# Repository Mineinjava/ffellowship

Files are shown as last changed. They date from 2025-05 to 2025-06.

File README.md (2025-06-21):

# ffellowship
Frequency Fellowship: Examining Radio Wave Propagation from a High Altitude Balloon
---

This is a project for Hack Club's [Apex](https://apex.hackclub.com),
made by:
- [Marcus Kauffman](https://kauffman.tools) KN6UYL (@mineinjava)
- Hudson Hilal (@hhilal123)
- Joshua Truman (@jstruman4929)

We initially had two project ideas for Apex: this and dropping what was
effectively a lawn dart from 100,000 feet. After the lawn dart project
was rejected, we submitted this project.

Many high altitude balloons (HABs) have been launched, almost all of
which have some sort of tracker that transmits the balloon's location.
These transmissions are received by stations on the ground and then
uploaded to the internet, from which we can view the locations of
receiving stations for analysis. Our goal for this project is to study
the differences between different tracker design techniques,
specifically:

- Does radio band selection influence likelihood of reception?
    - Receiving stations on the 2m band are much more common than those
      on the 20m band, but 20m transmissions theoretically travel
      farther.
- There are three common methods of modulating signals:
    - Connecting to a dedicated radio for transmission
    - Using a MS5351M or similar clock generator IC
    - Using [fancy PLL](https://github.com/kaduhi/pico-fractional-pll)
      to "bit-bang" the radio waveform

    **Question: do these three modulation methods have a significant
    difference in quality and therefore propagation?**
- How do different antenna designs affect propagation.

Due to customs issues, we were only able to test the PLL tracker 
with three antenna wavelengths. Two of the frequencies had issues 
(unresolved ATM), so we instead analyzed the effect of height on 
radio wave propagation.

As suggested above, this project can easily be divided into three
"sub-projects":

## 1. Use of the MS5351M Clock Generator IC.

This subproject revolves around the MS5351M clock generator. It features
a custom PCB. Note that this tracker will transmit on both the 20m and
2m bands because the MS5351M has multiple clock generators.

This tracker has quite a few features, many of which are to support
ultra-low power operation, as is common with this style of tracker:

- GPS
- Temperature/pressure sensor
- Shunt
- 3v3 buck-boost converter
- power supervisor to restart the pico
- Sensors can be powered off to conserve power.

This PCB is designed around the Raspberry Pi Pico due to its rigorous
testing and ease of integration. It also features mainly 1206 components
to aid in manual reflow soldering of the PCB.

See the dPicoTracker/ directory for more info.





## 2. Use of PLL:

This subproject uses the Raspberry Pi Pico to generate RF signals,
*without the use of a dedicated radio/chip*. It is by far the simplest
design and features a power supervisor, optional low-pass filter, 
battery measurement circuitry, as well as a GPS which is essential 
for correcting oscillator drift.





## 3. Use of a Dedicated HT Radio.

This subproject uses a Raspberry Pi Zero W and a custom PCB to connect
to a HT, which will be stripped down to save weight. 

The PCB consists of a voltage regulator to power the Pi and a 555 timer
circuit to ensure that transmissions are limited in time (in case
of a software crash).





## Integration:

*coming soon*

## Project Status:

*coming soon*

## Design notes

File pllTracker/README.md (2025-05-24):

# Tracker using PLL

This tracker uses fractional PLL to generate RF on the 20m band.

## BOM:

| Id  | Designator | Footprint | Quantity | Designation | Supplier and ref |
|-----|---|---|---|---|---|
| 1 | C15 | C_1206_3216Metric | 1 | 300pF | C5449026 |
| 2 | C14,C16 | C_1206_3216Metric | 2 | 180pF | C3832761 |
| 3 | R6 | C_1206_3216Metric | 1 | 100kΩ | C137393 |
| 4 | U7 | SOT-23_ONS | 1 | MAX809STRG | C9965 |
| 6 | R1 | C_1206_3216Metric | 1 | 10kΩ | C132649 |
| 7 | L5,L4 | L_1206_3216Metric | 2 | 560nH | C13585 |
| 10  | IC1 | ATGM336H5N31 | 1 | ATGM336H-5N31 | C2940946 |
| 11  | C8 | C_1206_3216Metric | 2 | 100nF | C137393 |
| 13  | Q1, Q2 | Q_SOT-23 | 1 | AO3401A | C15127 |
| 13  | C7 | C_1206_3216Metric | 1 | 1nF | C23631 |
| 14  | R5 | D_1206_3216Metric | 1 | 200kΩ | C114937 |

Additionally:
- 1 GPS antenna
- 1 20m antenna
- 1 Raspberry Pi Pico

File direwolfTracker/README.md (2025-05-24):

# Direwolf-powered Tracker

This tracker uses direwolf to communicate with an external radio like a
HT.

## BOM:

| Id  | Designator | Footprint | Quantity | Designation | Supplier and ref |
|-----|---|---|---|---|---|
| 1 | C2, C1, C3 | C_1206_3216Metric | 3 | 10µF | C13585 |
| 3 | Q1 | Q_SOT-23 | 1 | MMBT2222A | C82460 |
| 4 | C20, C19, C21 | C_1206_3216Metric | 3 | 100nF | C82460 |
| 7 | U1 | Texas_R-PDSO-G6 | 1 | TPS61222DCK | C116461 |
| 9 | R1 | R_1206_3216Metric | 1 | 10kΩ | C132649 |
| 10  | R3 | R_1206_3216Metric | 1 | 2.7kΩ | C2930416 |
| 12  | IC1 | ATGM336H5N31 | 1 | ATGM336H-5N31 | C2940946 |
| 13  | R2 | R_1206_3216Metric | 1 | 100kΩ | C2930416 |
| 14  | U2 | DIP-8_W7.62mm | 1 | ICM7555xP | C22461592 |
| 15  | R4 | R_1206_3216Metric | 1 | 1MΩ | C108083 |
| 16  | L1 | L_1206_3216Metric | 1 | 4.7µH | C13585 |

Additionally:
- 1 Raspberry Pi Zero
- 1 GPS Antenna
- 1 micro usb sound card
- 1 TRRS 3.5mm cable
- 1 TRS 3.5mm cable
- 1 TRS 2.5mm cable
- 1 external radio

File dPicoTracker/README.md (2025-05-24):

# Tracker With MS5351M IC

This tracker uses the MS5351M IC to generate RF.

## BOM:

| Id  | Designator | Footprint | Quantity | Designation | Supplier and ref | 
|-----|---|---|---|---|---|
| 1 | L1 | L_1206_3216Metric | 1 | 4.7µH | C13585 |
| 2 | C14, C16 | C_1206_3216Metric | 2 | 18pF | C565686 |
| 3 | L4, L5 | L_1206_3216Metric | 2 | 56nH | C13585 |
| 4 | U7 | SOT-23_ONS | 1 | MAX809STRG | C9965 |
| 6 | U8 | Bosch_LGA-8_2x2.5mm_P0.65mm | 1 | BMP280 | C83291 |
| 7 | Y1 | MSOP-10_3x3mm_P0.5mm | 1 | Si5351A-B-GT | C1509083 |
| 8 | C9, C19, C1, C8, C17, C18, C10 | C_1206_3216Metric | 7 | 100nF | C24497 |
| 10  | Y2 | Crystal_SMD_2520-4Pin_2.5x2.0mm | 1 | C132296 | C132296 |
| 11  | L3, L2 | L_1206_3216Metric | 2 | 560nH | C13585 |
| 12  | R6 | C_1206_3216Metric | 1 | 100kΩ | C137393 |
| 13  | Q1, Q2 | Q_SOT-23 | 2 | AO3401A | C15127 |
| 15  | R8, R14, R15, R11, R9, R12 | R_1206_3216Metric | 6 | 10kΩ | C132649 |
| 16  | C15 | C_1206_3216Metric | 1 | 30pF | C1905 |
| 17  | C12 | C_1206_3216Metric | 1 | 300pF | C5449026 |
| 18  | C5 | C_1206_3216Metric | 1 | 10µF | C13585 |
| 19  | C11, C13 | C_1206_3216Metric | 2 | 180pF | C3832761 |
| 20  | IC1 | ATGM336H5N31 | 1 | ATGM336H-5N31 | C2940946 |
| 21  | U3, U4 | SOT-23-3_L2.9-W1.6-P1.90-LS2.8-BR | 2 | CJ431 | C3113 |
| 22  | R7 | C_1206_3216Metric | 1 | 10kΩ | C132649 |
| 23  | U5 | Texas_R-PDSO-G6 | 1 | TPS61221DCK | C2865756 |
| 24  | C7 | C_1206_3216Metric | 1 | 1nF | C23631 |
| 25  | R5 | D_1206_3216Metric | 1 | 200kΩ | C114937 |

Additionally:
- 1x GPS antenna
- 1x 2m antenna
- 1x 20m antenna
- 1x Raspberry Pi Pico

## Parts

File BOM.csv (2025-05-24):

Comment | Designator | Footprint | LCSC Part # | Quantity
4.7µH | L1 | L_1206_3216Metric | C13585 | 2
18pF | C14 C16 | C_1206_3216Metric | C565686 | 2
56nH | L4 L5 | L_1206_3216Metric | C13585 | 2
MAX809STRG | U7 | U_SOT-23_ONS | C9965 | 2
BMP280 | U8 | Bosch_LGA-8_2x2.5mm_P0.65mm | C83291 | 1
Si5351A-B-GT | Y1 | MSOP-10_3x3mm_P0.5mm | C1509083 | 1
100nF | C9 C19 C1 C8 C17 C18 C10 C20 C21 | C_1206_3216Metric | C24497 | 10
C132296 | Y2 | Crystal_SMD_2520-4Pin_2.5x2.0mm | C132296 | 1
560nH | L2 L3 L4 L5 | L_1206_3216Metric | C13585 | 4
100kΩ | R6 R2 | C_1206_3216Metric | C137393 | 2
AO3401A | Q1 Q2 Q1 | Q_SOT-23 | C15127 | 3
10kΩ | R1 R7 R8 R9 R11 R12 R14 | R_1206_3216Metric | C132649 | 8
30pF | C15 | C_1206_3216Metric | C1905 | 1
300pF | C12 C15 | C_1206_3216Metric | C5449026 | 2
10µF | C2 C1 C3 C5 | C_1206_3216Metric | C13585 | 4
180pF | C11 C13 C14 C16 | C_1206_3216Metric | C3832761 | 4
ATGM336H-5N31 | IC1 IC1 IC1 | ATGM336H5N31 | C2940946 | 3
CJ431 | U3 U4 | SOT-23-3_L2.9-W1.6-P1.90-LS2.8-BR | C3113 | 2
TPS61221DCK | U5 | Texas_R-PDSO-G6 | C2865756 | 1
1nF | C7 C7 | C_1206_3216Metric | C23631 | 2
200kΩ | R5 R5 | D_1206_3216Metric | C114937 | 2
MMBT2222A | Q1 | Q_SOT-23 | C82460 | 1
TPS61222DCK | U1 | Texas_R-PDSO-G6 | C116461 | 1
2.7kΩ | R3 | R_1206_3216Metric | C2930416 | 1
ICM7555xP | U2 | DIP-8_W7.62mm | C22461592 | 1
1MΩ | R4 | R_1206_3216Metric | C108083 | 1

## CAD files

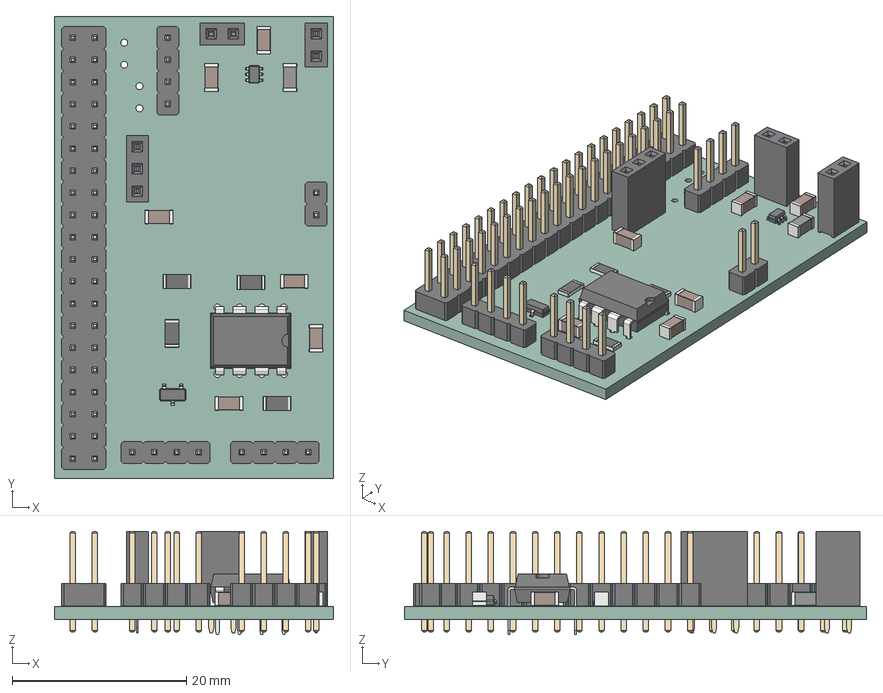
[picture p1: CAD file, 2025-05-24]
direwolfTracker/direwolfTracker.step
32.0 x 53.0 x 11.8 mm
C_1206_3216Metric x 6
PinSocket_1x02_P2.54mm_Vertical x 2
Q_SOT-23
PinHeader_1x04_P2.54mm_Vertical x 3
PinSocket_1x03_P2.54mm_Vertical
SOT-363_SC-70-6
R_1206_3216Metric x 4
PinHeader_1x02_P2.54mm_Vertical
DIP-8_W7.62mm
L_1206_3216Metric
PinHeader_2x20_P2.54mm_Vertical
direwolfTracker_PCB

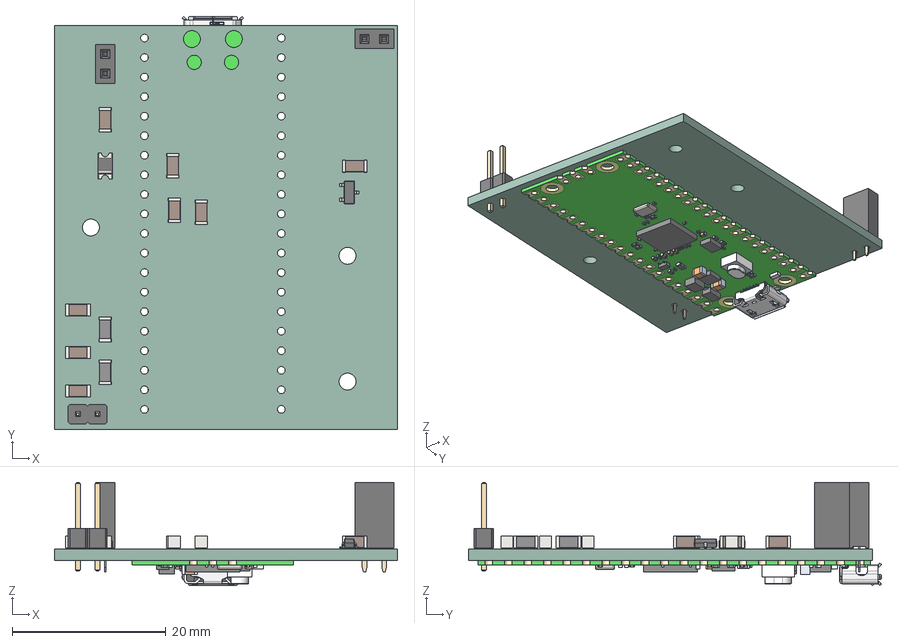
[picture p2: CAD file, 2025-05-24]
pllTracker/pllTracker.step
44.6 x 53.7 x 13.4 mm
C_1206_3216Metric x 8
Q_SOT-23
PinSocket_1x02_P2.54mm_Vertical x 2
L_1206_3216Metric x 2
PinHeader_1x02_P2.54mm_Vertical
D_1206_3216Metric
PCB, Raspberry Pi Pico-R3
MicroUSB Port, Raspberry Pi Pico-R3
RP2040 Microcontroller, Raspberry Pi Pico-R3
SW1, Tact Switch, Raspberry Pi Pico-R3
D1, Diode, Schottky, Raspberry Pi Pico-R3
D2, QSME-C194, LED, Raspberry Pi Pico-R3
L1, Inductor, Raspberry Pi Pico-R3
U2, RT6150B-33GQW, Buck Boost Converter, Raspberry Pi Pico-R3
U3, W25Q16JVUXIQ, Serial NOR Flash 16 Mbit, Raspberry Pi Pico-R3
Q1, MOSFET, DMG1012T, Raspberry Pi Pico-R3
X1, X12M000000S096, 12 Mhz Crystal Resonator, Raspberry Pi Pico-R3
SMD Resistor, Configurable, Raspberry Pi Pico-R3_R1
SMD Resistor, Configurable, Raspberry Pi Pico-R3_R2
SMD Resistor, Configurable, Raspberry Pi Pico-R3_R3
SMD Resistor, Configurable, Raspberry Pi Pico-R3_R4
SMD Resistor, Configurable, Raspberry Pi Pico-R3_R5
SMD Resistor, Configurable, Raspberry Pi Pico-R3_R6
SMD Resistor, Configurable, Raspberry Pi Pico-R3_R7
SMD Resistor, Configurable, Raspberry Pi Pico-R3_R8
SMD Resistor, Configurable, Raspberry Pi Pico-R3_R9
SMD Resistor, Configurable, Raspberry Pi Pico-R3_R10
SMD Resistor, Configurable, Raspberry Pi Pico-R3_R11
SMD Resistor, Configurable, Raspberry Pi Pico-R3_R12
SMD Resistor, Configurable, Raspberry Pi Pico-R3_R13
SMD Resistor, Configurable, Raspberry Pi Pico-R3_R14
SMD Resistor, Configurable, Raspberry Pi Pico-R3_R15
SMD Capacitor, Configurable, Raspberry Pi Pico-R3_C1
SMD Capacitor, Configurable, Raspberry Pi Pico-R3_C2
SMD Capacitor, Configurable, Raspberry Pi Pico-R3_C3
SMD Capacitor, Configurable, Raspberry Pi Pico-R3_C4
SMD Capacitor, Configurable, Raspberry Pi Pico-R3_C5
SMD Capacitor, Configurable, Raspberry Pi Pico-R3_C6
SMD Capacitor, Configurable, Raspberry Pi Pico-R3_C7
SMD Capacitor, Configurable, Raspberry Pi Pico-R3_C8
SMD Capacitor, Configurable, Raspberry Pi Pico-R3_C9
SMD Capacitor, Configurable, Raspberry Pi Pico-R3_C10
SMD Capacitor, Configurable, Raspberry Pi Pico-R3_C11
SMD Capacitor, Configurable, Raspberry Pi Pico-R3_C12
SMD Capacitor, Configurable, Raspberry Pi Pico-R3_C13
SMD Capacitor, Configurable, Raspberry Pi Pico-R3_C14
SMD Capacitor, Configurable, Raspberry Pi Pico-R3_C15
SMD Capacitor, Configurable, Raspberry Pi Pico-R3_C16
SMD Capacitor, Configurable, Raspberry Pi Pico-R3_C17
SMD Capacitor, Configurable, Raspberry Pi Pico-R3_C18
pllTracker_PCB

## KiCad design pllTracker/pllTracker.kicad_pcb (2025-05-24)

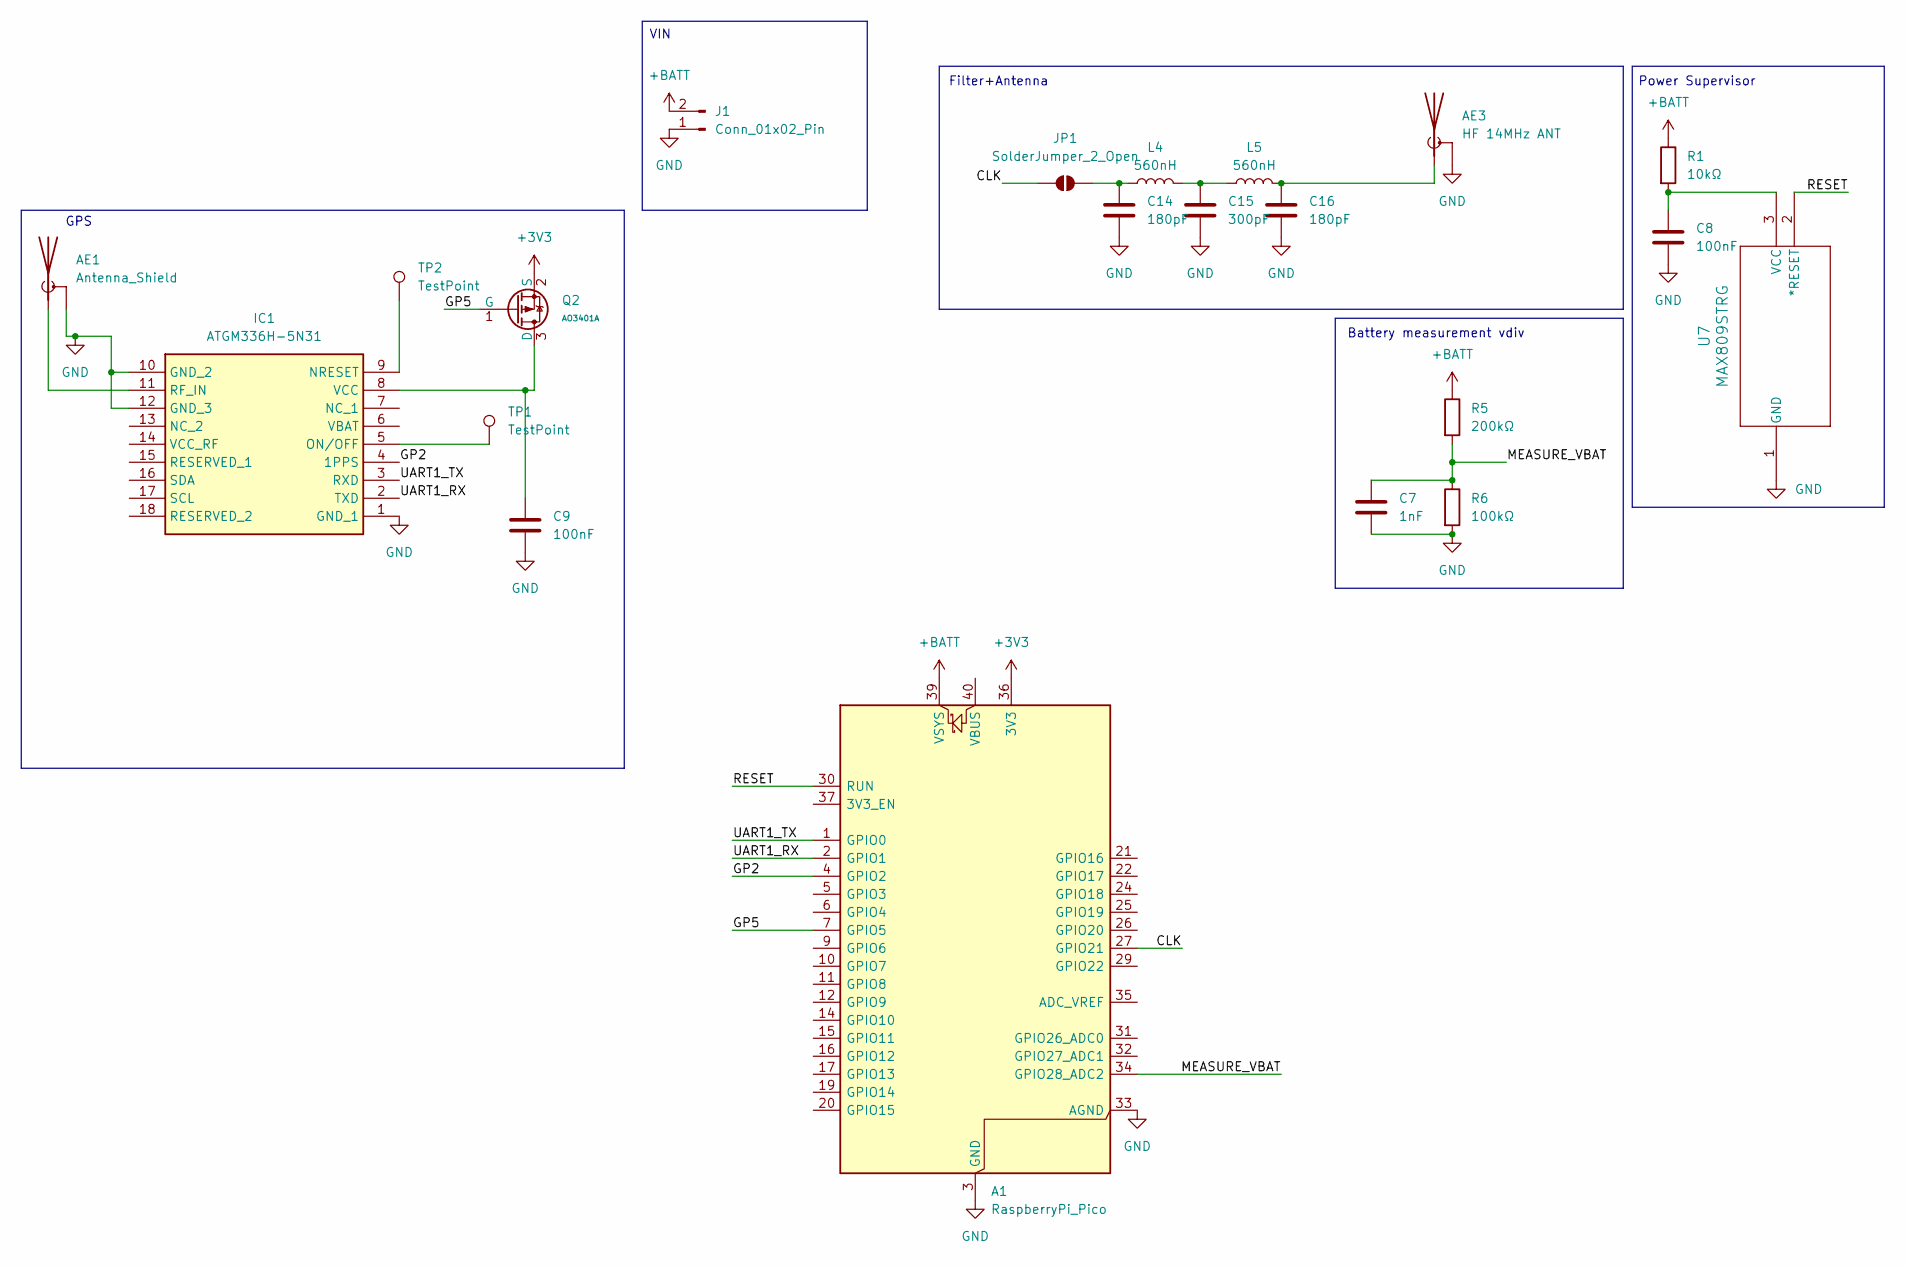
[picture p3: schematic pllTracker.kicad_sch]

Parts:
A1: RaspberryPi_Pico; RaspberryPi_Pico_Common_Unspecified
AE1: Antenna_Shield; PinSocket_1x02_P2.54mm_Vertical
AE3: HF 14MHz ANT; PinHeader_1x02_P2.54mm_Vertical
C7: 1nF; C_1206_3216Metric
C8, C9: 100nF; C_1206_3216Metric
C14, C16: 180pF; C_1206_3216Metric
C15: 300pF; C_1206_3216Metric
IC1: ATGM336H-5N31; ATGM336H5N31; Manufacturer_Part_Number ATGM336H-5N31
J1: Conn_01x02_Pin; PinSocket_1x02_P2.54mm_Vertical
JP1: SolderJumper_2_Open; SolderJumper-2_P1.3mm_Open_Pad1.0x1.5mm
L4, L5: 560nH; L_1206_3216Metric
Q2: AO3401A; Q_SOT-23; Part AO3401A; LCSC C15127
R1: 10kΩ; C_1206_3216Metric
R5: 200kΩ; D_1206_3216Metric
R6: 100kΩ; C_1206_3216Metric
TP1, TP2: TestPoint; TestPoint_Pad_D1.5mm
U7: MAX809STRG; SOT-23_ONS

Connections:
+3V3: A1.36 (3V3), Q2.2 (S)
+BATT: A1.39 (VSYS), J1.2, R1.1, R5.1
/CLK: A1.27 (GPIO21), JP1.1 (A)
/GP2: A1.4 (GPIO2), IC1.4 (1PPS)
/GP5: A1.7 (GPIO5), Q2.1 (G)
/MEASURE_VBAT: A1.34 (GPIO28_ADC2), C7.2, R5.2, R6.1
/RESET: A1.30 (RUN), U7.2 (*RESET)
/UART1_RX: A1.2 (GPIO1), IC1.2 (TXD)
/UART1_TX: A1.1 (GPIO0), IC1.3 (RXD)
GND: A1.3 (GND), A1.8 (GND), A1.13 (GND), A1.18 (GND), A1.23 (GND), A1.28 (GND), A1.33 (AGND), A1.38 (GND), AE1.2 (Shield), AE3.2 (Shield), C7.1, C8.2, C9.2, C14.2, C15.2, C16.2, IC1.1 (GND_1), IC1.10 (GND_2), IC1.12 (GND_3), J1.1, R6.2, U7.1 (GND)
unnamed: AE1.1 (A), IC1.11 (RF_IN)
unnamed: AE3.1 (A), C16.1, L5.2
unnamed: C15.1, L4.2, L5.1
unnamed 13: IC1.9 (NRESET), TP2.1; also elsewhere on the board
unnamed 14: IC1.5 (ON/OFF), TP1.1; also elsewhere on the board
unnamed: C9.1, IC1.8 (VCC), Q2.3 (D)
unnamed: C14.1, JP1.2 (B), L4.1
unnamed: C8.1, R1.2, U7.3 (VCC)

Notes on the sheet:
Power Supervisor
VIN
GPS
Filter+Antenna
Battery measurement vdiv

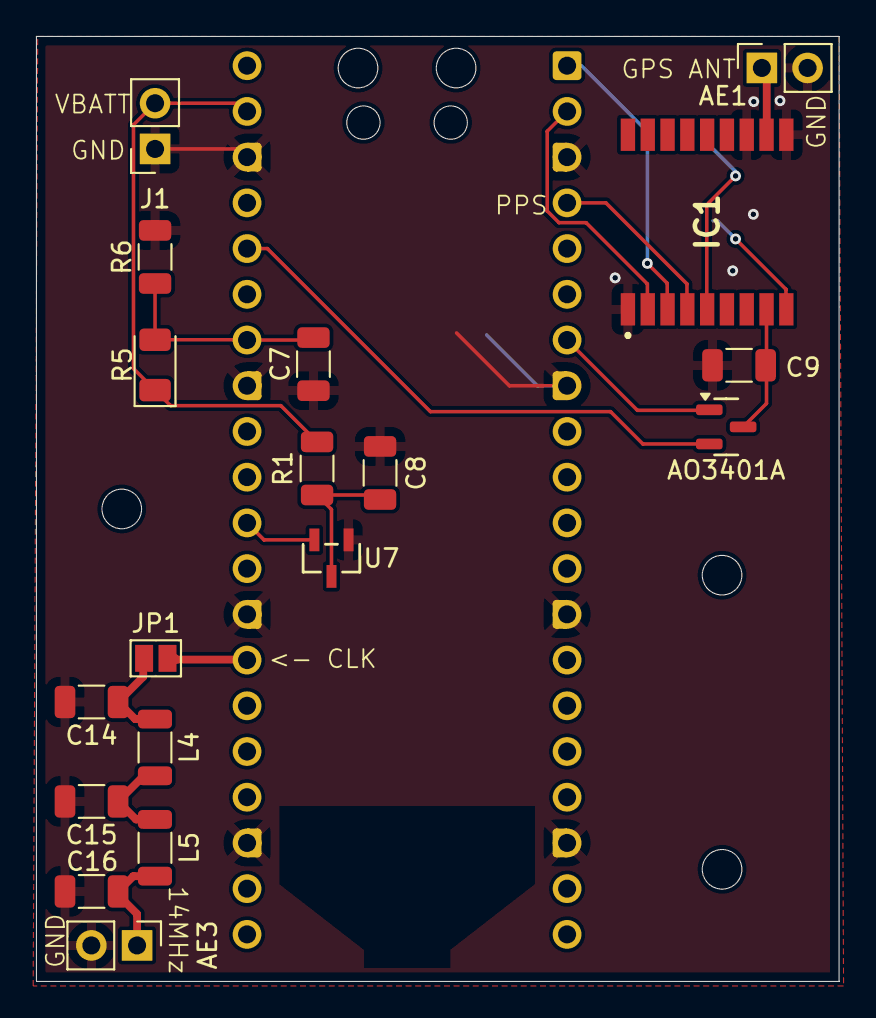
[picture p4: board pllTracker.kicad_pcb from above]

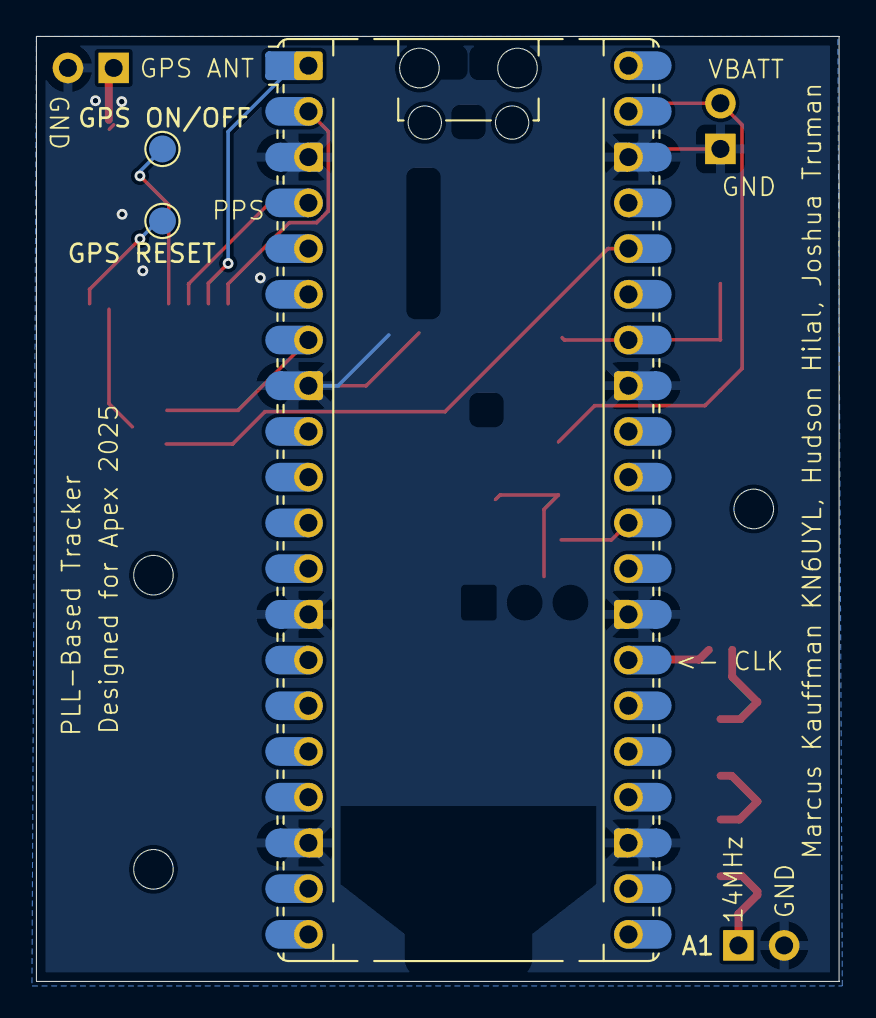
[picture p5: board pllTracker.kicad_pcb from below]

Board: 2 copper layers, 44.6 x 52.5 mm, 21 parts (3 on the bottom side), 18 nets.

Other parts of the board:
GPS ON/OFF: TestPoint; TestPoint_Pad_D1.5mm
GPS RESET: TestPoint; TestPoint_Pad_D1.5mm

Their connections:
unnamed 13: GPS RESET.1; also elsewhere on the board
unnamed 14: GPS ON/OFF.1; also elsewhere on the board

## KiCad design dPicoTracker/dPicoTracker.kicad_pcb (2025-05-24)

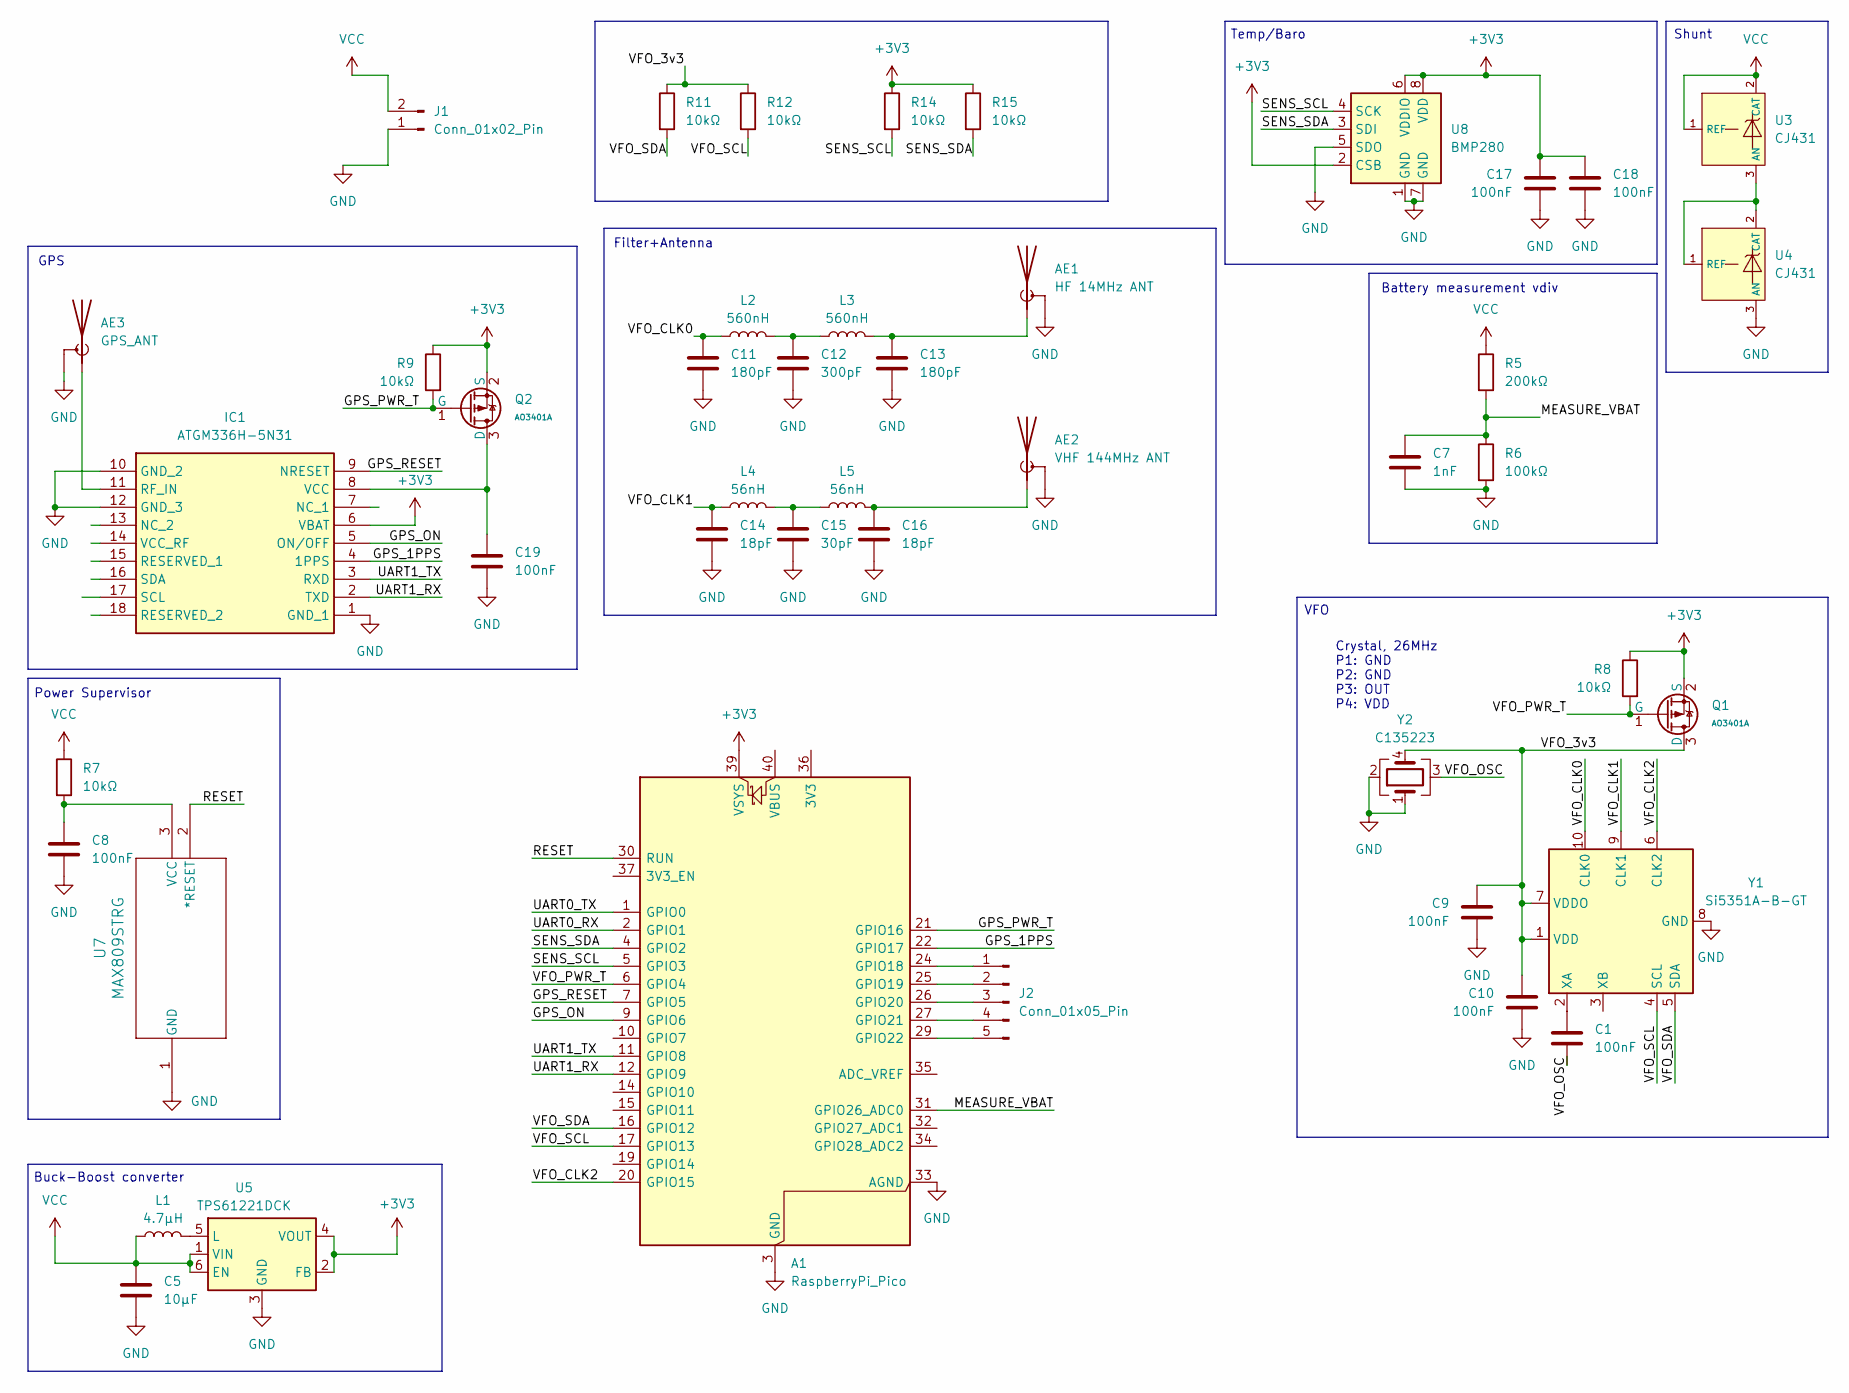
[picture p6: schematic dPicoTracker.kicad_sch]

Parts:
A1: RaspberryPi_Pico; RaspberryPi_Pico_Common_Unspecified
AE1: HF 14MHz ANT; PinHeader_1x02_P2.54mm_Vertical
AE2: VHF 144MHz ANT; PinHeader_1x02_P2.54mm_Vertical
AE3: GPS_ANT; PinHeader_1x02_P2.54mm_Vertical
C1, C8, C9, C10, C17, C18, C19: 100nF; C_1206_3216Metric
C5: 10µF; C_1206_3216Metric
C7: 1nF; C_1206_3216Metric
C11, C13: 180pF; C_1206_3216Metric
C12: 300pF; C_1206_3216Metric
C14, C16: 18pF; C_1206_3216Metric
C15: 30pF; C_1206_3216Metric
IC1: ATGM336H-5N31; ATGM336H5N31; Manufacturer_Part_Number ATGM336H-5N31
J1: Conn_01x02_Pin; PinSocket_1x02_P2.00mm_Vertical
J2: Conn_01x05_Pin; PinSocket_1x05_P2.54mm_Vertical
L1: 4.7µH; L_1206_3216Metric
L2, L3: 560nH; L_1206_3216Metric
L4, L5: 56nH; L_1206_3216Metric
Q1, Q2: AO3401A; Q_SOT-23; Part AO3401A; LCSC C15127
R5: 200kΩ; D_1206_3216Metric
R6: 100kΩ; C_1206_3216Metric
R7: 10kΩ; C_1206_3216Metric
R8, R9, R11, R12, R14, R15: 10kΩ; R_1206_3216Metric
U3, U4: CJ431; SOT-23-3_L2.9-W1.6-P1.90-LS2.8-BR; Output Voltage 2.5V~36V; Tolerance ±0.5%; Part CJ431; LCSC C3113
U5: TPS61221DCK; Texas_R-PDSO-G6
U7: MAX809STRG; SOT-23_ONS
U8: BMP280; Bosch_LGA-8_2x2.5mm_P0.65mm_ClockwisePinNumbering
Y1: Si5351A-B-GT; MSOP-10_3x3mm_P0.5mm
Y2: C135223; Crystal_SMD_2520-4Pin_2.5x2.0mm

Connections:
+3V3: A1.39 (VSYS), C17.1, C18.1, IC1.6 (VBAT), Q1.2 (S), Q2.2 (S), R8.1, R9.1, R14.1, R15.1, U5.2 (FB), U5.4 (VOUT), U8.2 (CSB), U8.6 (VDDIO), U8.8 (VDD)
/GPS_1PPS: A1.22 (GPIO17), IC1.4 (1PPS)
/GPS_ON: A1.9 (GPIO6), IC1.5 (ON/OFF)
/GPS_PWR_T: A1.21 (GPIO16), Q2.1 (G), R9.2
/GPS_RESET: A1.7 (GPIO5), IC1.9 (NRESET)
/MEASURE_VBAT: A1.31 (GPIO26_ADC0), C7.2, R5.2, R6.1
/RESET: A1.30 (RUN), U7.2 (*RESET)
/SENS_SCL: A1.5 (GPIO3), R14.2, U8.4 (SCK)
/SENS_SDA: A1.4 (GPIO2), R15.2, U8.3 (SDI)
/UART0_RX: A1.2 (GPIO1)
/UART0_TX: A1.1 (GPIO0)
/UART1_RX: A1.12 (GPIO9), IC1.2 (TXD)
/UART1_TX: A1.11 (GPIO8), IC1.3 (RXD)
/VFO_3v3: C9.1, C10.1, Q1.3 (D), R11.1, R12.1, Y1.1 (VDD), Y1.7 (VDDO), Y2.4
/VFO_CLK0: C11.1, L2.1, Y1.10 (CLK0)
/VFO_CLK1: C14.1, L4.1, Y1.9 (CLK1)
/VFO_CLK2: A1.20 (GPIO15), Y1.6 (CLK2)
/VFO_OSC: C1.1, Y2.3
/VFO_PWR_T: A1.6 (GPIO4), Q1.1 (G), R8.2
/VFO_SCL: A1.17 (GPIO13), R12.2, Y1.4 (SCL)
/VFO_SDA: A1.16 (GPIO12), R11.2, Y1.5 (SDA)
GND: A1.3 (GND), A1.8 (GND), A1.13 (GND), A1.18 (GND), A1.23 (GND), A1.28 (GND), A1.33 (AGND), A1.38 (GND), AE1.2 (Shield), AE2.2 (Shield), AE3.2 (Shield), C5.2, C7.1, C8.2, C9.2, C10.2, C11.2, C12.2, C13.2, C14.2, C15.2, C16.2, C17.2, C18.2, C19.2, IC1.1 (GND_1), IC1.10 (GND_2), IC1.12 (GND_3), J1.1, R6.2, U4.3 (AN), U5.3 (GND), U7.1 (GND), U8.1 (GND), U8.5 (SDO), U8.7 (GND), Y1.8 (GND), Y2.1, Y2.2
unnamed: A1.24 (GPIO18), J2.1
unnamed: A1.25 (GPIO19), J2.2
unnamed: A1.26 (GPIO20), J2.3
unnamed: A1.27 (GPIO21), J2.4
unnamed: A1.29 (GPIO22), J2.5
unnamed: AE1.1 (A), C13.1, L3.2
unnamed: AE2.1 (A), C16.1, L5.2
unnamed: AE3.1 (A), IC1.11 (RF_IN)
unnamed: C12.1, L2.2, L3.1
unnamed: C15.1, L4.2, L5.1
unnamed: C19.1, IC1.8 (VCC), Q2.3 (D)
unnamed: U3.3 (AN), U4.1 (REF), U4.2 (CAT)
unnamed: L1.2, U5.5 (L)
unnamed: C8.1, R7.2, U7.3 (VCC)
unnamed: C1.2, Y1.2 (XA)
VCC: C5.1, J1.2, L1.1, R5.1, R7.1, U3.1 (REF), U3.2 (CAT), U5.1 (VIN), U5.6 (EN)

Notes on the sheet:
Filter+Antenna
Buck-Boost converter
Battery measurement vdiv
GPS
Shunt
Crystal, 26MHz P1: GND P2: GND P3: OUT P4: VDD
Power Supervisor
VFO
Temp/Baro

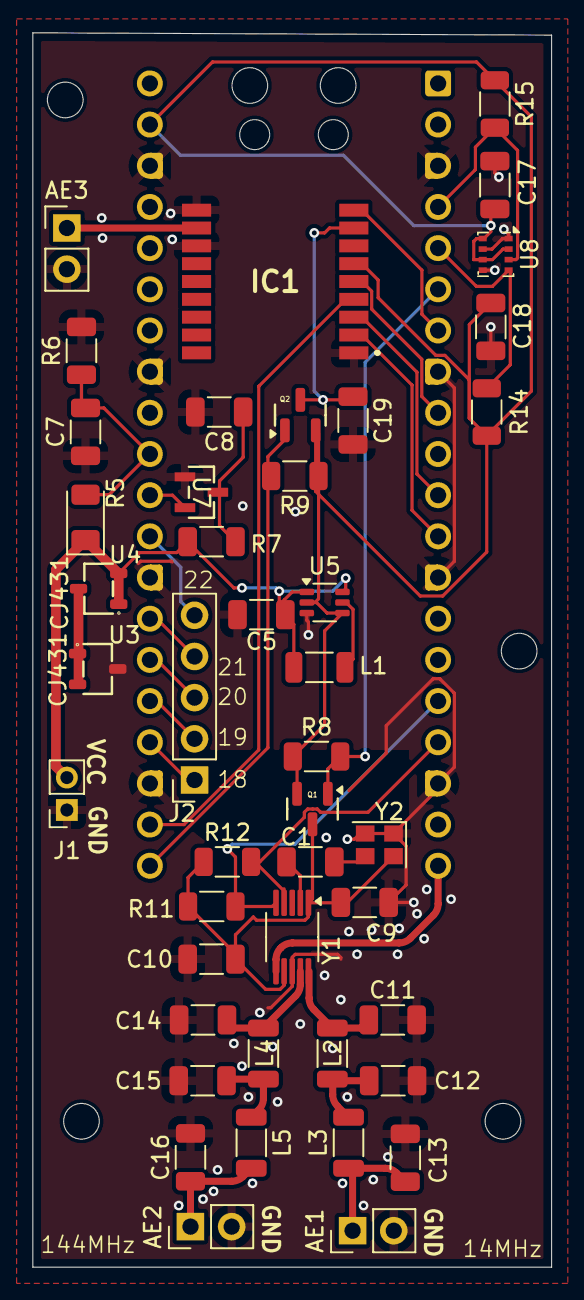
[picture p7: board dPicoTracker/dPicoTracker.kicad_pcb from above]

Board: 2 copper layers, 32.0 x 76.1 mm, 45 parts (1 on the bottom side), 36 nets.

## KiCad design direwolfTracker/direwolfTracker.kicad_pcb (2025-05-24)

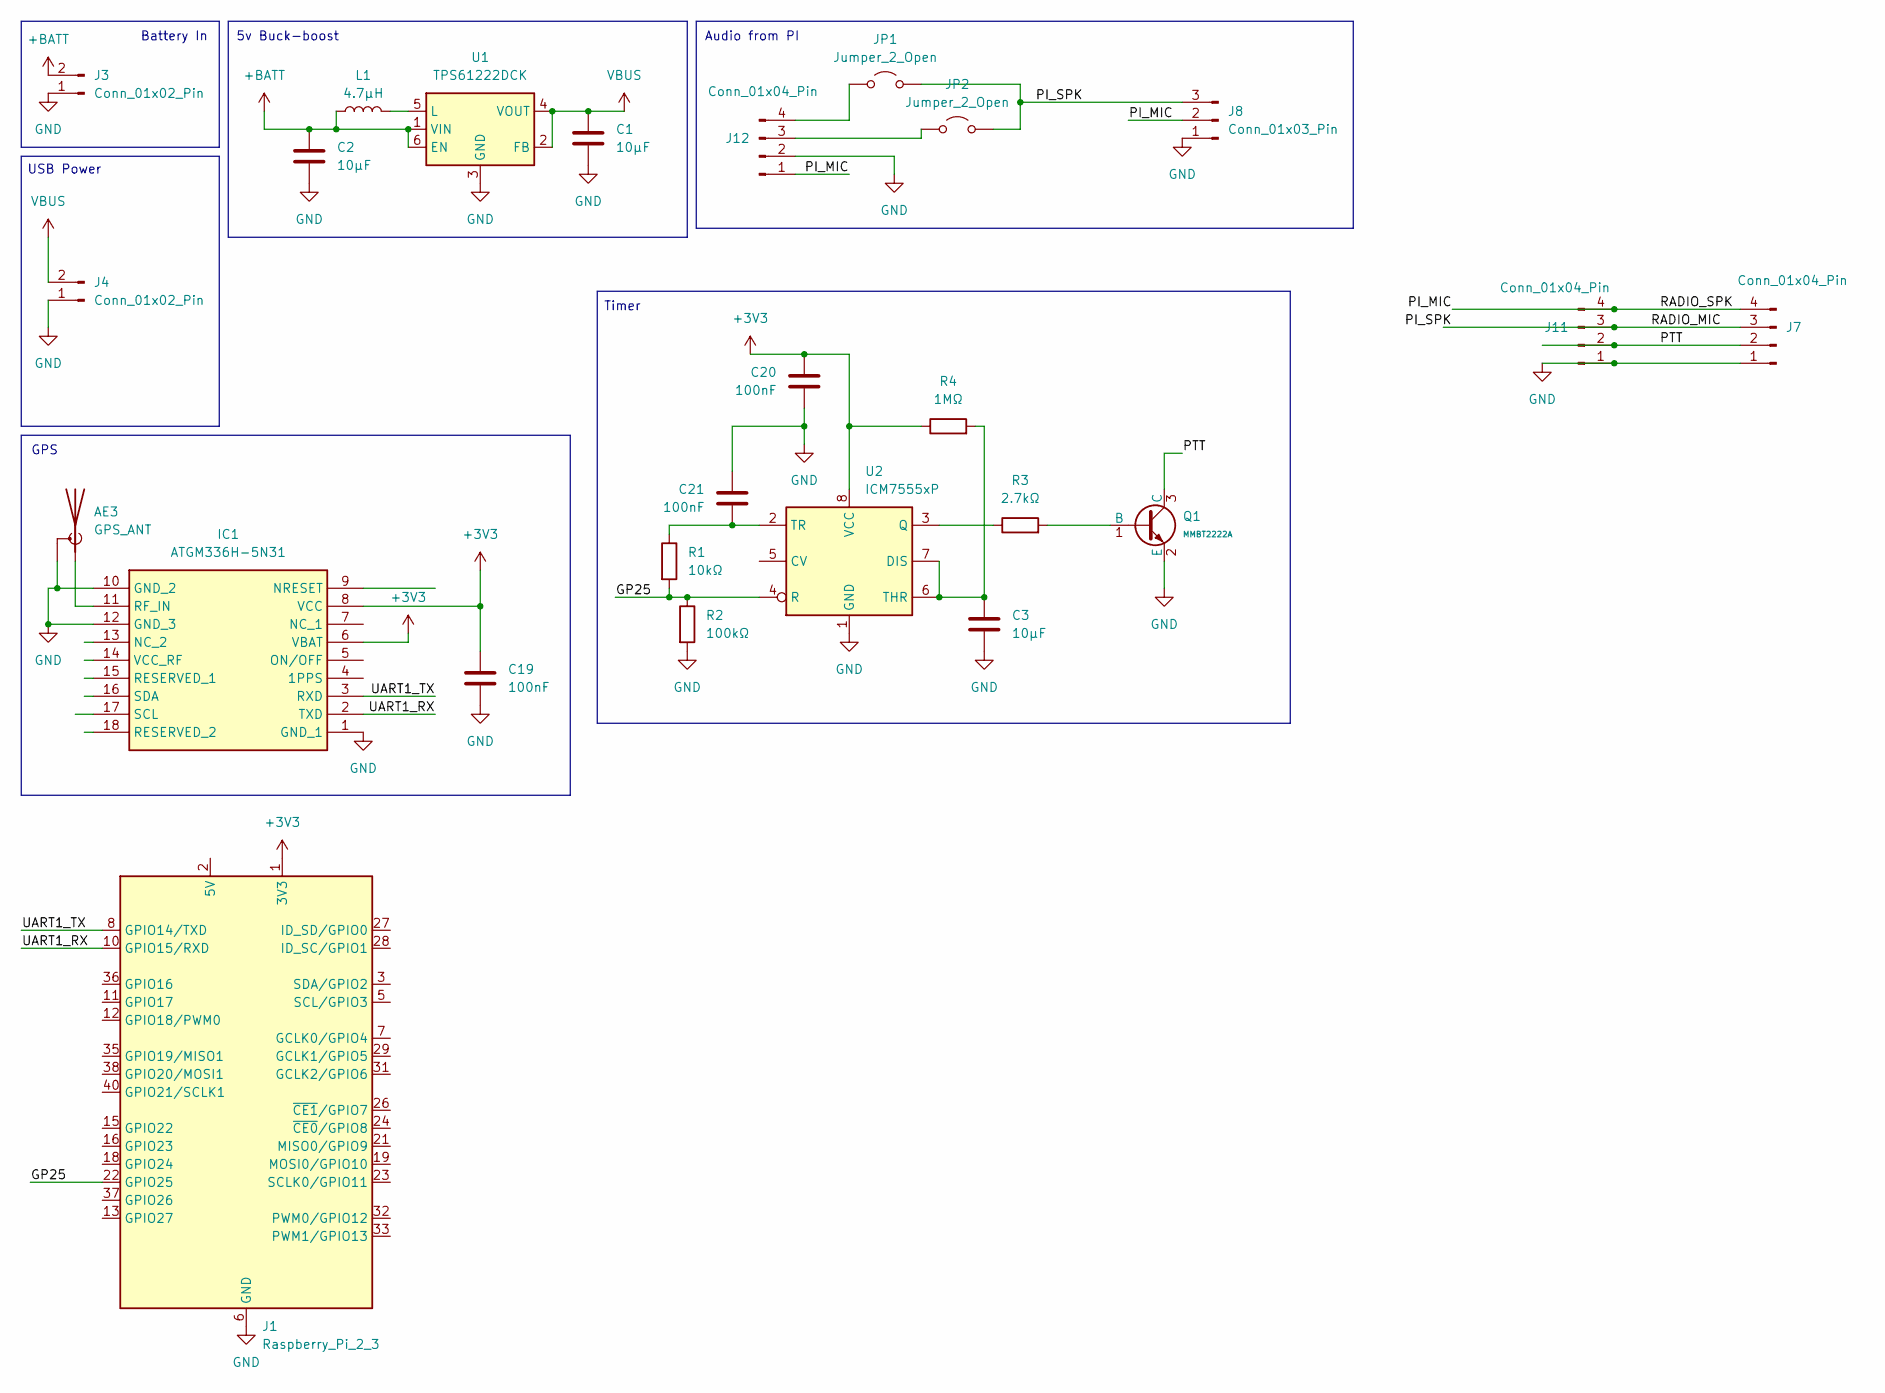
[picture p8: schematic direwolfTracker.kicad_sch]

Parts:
AE3: GPS_ANT; PinHeader_1x02_P2.54mm_Vertical
C1, C2, C3: 10µF; C_1206_3216Metric
C19, C20, C21: 100nF; C_1206_3216Metric
IC1: ATGM336H-5N31; ATGM336H5N31; Manufacturer_Part_Number ATGM336H-5N31
J1: Raspberry_Pi_2_3; PinHeader_2x20_P2.54mm_Vertical
J3, J4: Conn_01x02_Pin; PinSocket_1x02_P2.54mm_Vertical
J7, J11, J12: Conn_01x04_Pin; PinHeader_1x04_P2.54mm_Vertical
J8: Conn_01x03_Pin; PinSocket_1x03_P2.54mm_Vertical
JP1, JP2: Jumper_2_Open; TestPoint_2Pads_Pitch2.54mm_Drill0.8mm
L1: 4.7µH; L_1206_3216Metric
Q1: MMBT2222A; Q_SOT-23; Part MMBT2222A; LCSC C7420351
R1: 10kΩ; R_1206_3216Metric
R2: 100kΩ; R_1206_3216Metric
R3: 2.7kΩ; R_1206_3216Metric
R4: 1MΩ; R_1206_3216Metric
U1: TPS61222DCK; Texas_R-PDSO-G6
U2: ICM7555xP; DIP-8_W7.62mm

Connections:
+3V3: C19.1, C20.1, IC1.6 (VBAT), IC1.8 (VCC), J1.1 (3V3), J1.17 (3V3), R4.1, U2.8 (VCC)
+BATT: C2.1, J3.2, L1.1, U1.1 (VIN), U1.6 (EN)
/GP25: J1.22 (GPIO25), R1.2, R2.1, U2.4 (R)
/PI_MIC: J7.4, J8.2, J11.4, J12.1
/PI_SPK: J7.3, J8.3, J11.3, JP1.2 (B), JP2.2 (B)
/PTT: J7.2, J11.2, Q1.3 (C)
/UART1_RX: IC1.2 (TXD), J1.10 (GPIO15/RXD)
/UART1_TX: IC1.3 (RXD), J1.8 (GPIO14/TXD)
GND: AE3.2 (Shield), C1.2, C2.2, C3.2, C19.2, C20.2, C21.1, IC1.1 (GND_1), IC1.10 (GND_2), IC1.12 (GND_3), J1.6 (GND), J1.9 (GND), J1.14 (GND), J1.20 (GND), J1.25 (GND), J1.30 (GND), J1.34 (GND), J1.39 (GND), J3.1, J4.1, J7.1, J8.1, J11.1, J12.2, Q1.2 (E), R2.2, U1.3 (GND), U2.1 (GND)
unnamed: AE3.1 (A), IC1.11 (RF_IN)
unnamed: J1.2 (5V), J1.4 (5V)
unnamed: J12.3, JP2.1 (A)
unnamed: J12.4, JP1.1 (A)
unnamed: Q1.1 (B), R3.2
unnamed: L1.2, U1.5 (L)
unnamed: C3.1, R4.2, U2.6 (THR), U2.7 (DIS)
unnamed: R3.1, U2.3 (Q)
unnamed: C21.2, R1.1, U2.2 (TR)
VBUS: C1.1, J4.2, U1.2 (FB), U1.4 (VOUT)

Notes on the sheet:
Battery In
GPS
5v Buck-boost
Timer
Audio from PI
USB Power

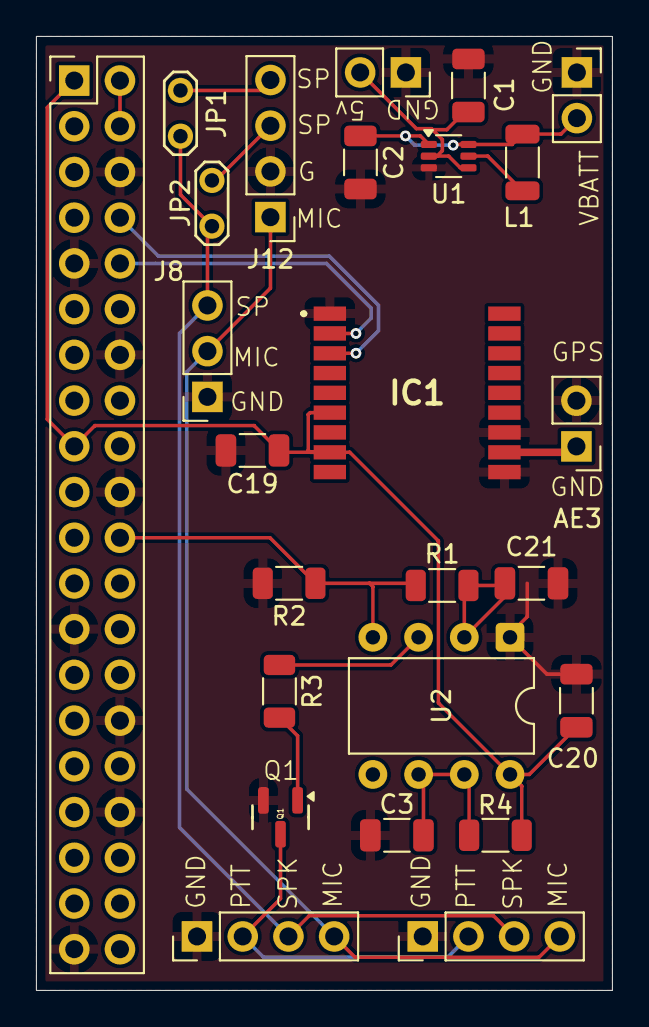
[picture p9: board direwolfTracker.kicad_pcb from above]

Board: 2 copper layers, 32.0 x 53.0 mm, 25 parts (0 on the bottom side), 19 nets.

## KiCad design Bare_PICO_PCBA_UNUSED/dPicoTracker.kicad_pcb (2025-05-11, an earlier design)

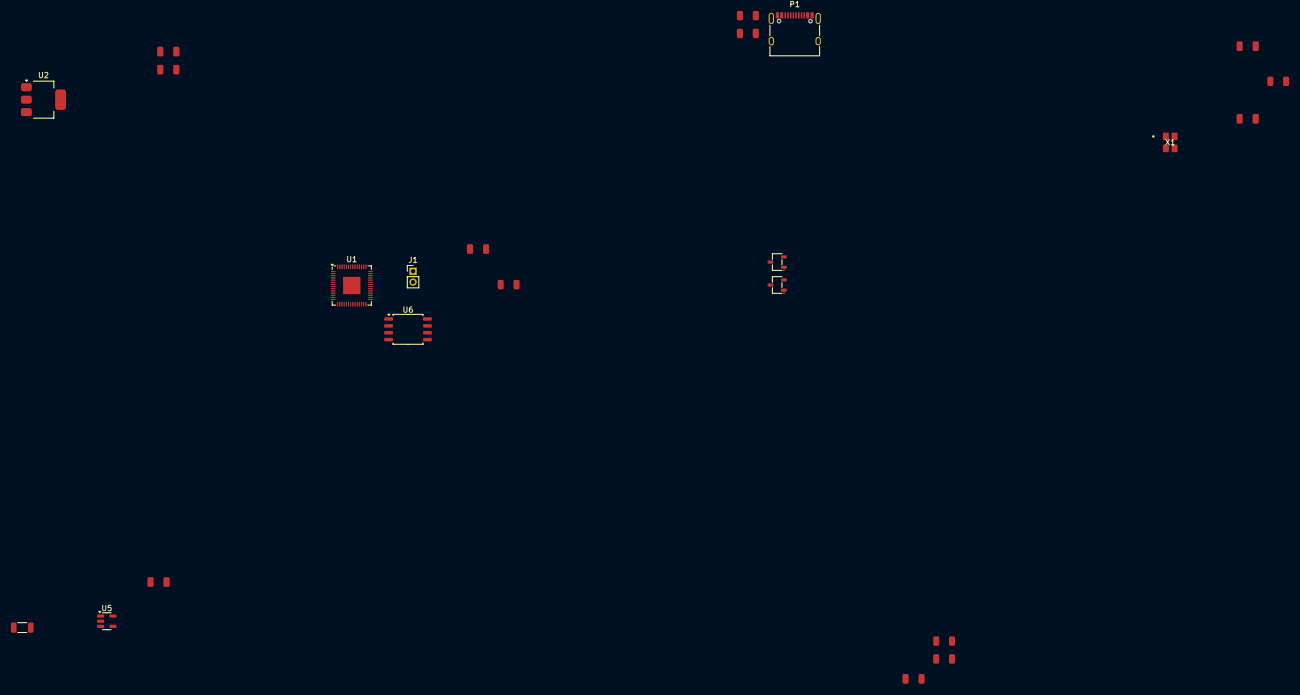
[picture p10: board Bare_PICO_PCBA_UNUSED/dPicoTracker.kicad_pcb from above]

Board: 2 copper layers, 23 parts (0 on the bottom side), 14 nets, no tracks yet.

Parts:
C1: 100nF; C_1206
C2, C6: 15pF; C_1206
C3, C4, C5: 10µF; C_1206
C7: 1nF; C_1206
J1: Conn_01x02_Pin; PinHeader_1x02_P2.00mm_Vertical
L1: 4.7µH; L_1206
P1: USB_C_Plug_USB2.0; USB_C_Receptacle_XKB_U262-16XN-4BVC11
R1, R2: 5.1kΩ; R_1206
R3, R4: 1kΩ; R_1206
R5: 200kΩ; R_1206
R6: 100kΩ; R_1206
U1: RP2040; QFN-56-1EP_7x7mm_P0.4mm_EP3.2x3.2mm
U2: NCP1117-3.3_SOT223; SOT-223-3_TabPin2
U3, U4: CJ431; SOT-23-3_L2.9-W1.6-P1.90-LS2.8-BR
U5: TPS61221DCK; SOT-23-5
U6: W25Q128JVS; SOIC-8_5.3x5.3mm_P1.27mm
X1: ABM8-272-T3; ABM8-272-T3_ABR

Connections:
+3V3: C1.1, C4.1, U2.2 (VO), U5.2 (FB), U5.4 (VOUT), U6.8 (VCC)
/MEASURE_VBAT: C7.2, R5.2, R6.1
/QSPI_SS: R3.2, U6.1 (~CS)
/XIN: C2.2, X1.1
GND: C1.2, C2.1, C3.2, C4.2, C5.2, C6.2, C7.1, J1.1, P1.A1 (GND), P1.A12 (GND), P1.B1 (GND), P1.B12 (GND), P1.S1 (SHIELD), R1.2, R2.2, R6.2, U2.1 (GND), U4.3 (AN), U5.3 (GND), U6.4 (GND), X1.2, X1.4
unnamed: C6.1, R4.1, X1.3
unnamed: J1.2, R3.1
unnamed: P1.A5 (CC), R1.1, R2.1
unnamed: U1.23 (DVDD), U1.50 (DVDD)
unnamed: U1.1 (IOVDD), U1.10 (IOVDD), U1.22 (IOVDD), U1.33 (IOVDD), U1.42 (IOVDD), U1.49 (IOVDD)
unnamed: U3.3 (AN), U4.1 (REF), U4.2 (CAT)
unnamed: L1.2, U5.5 (L)
VBUS: C3.1, C5.1, L1.1, P1.A4 (VBUS), P1.A9 (VBUS), P1.B4 (VBUS), P1.B9 (VBUS), R5.1, U2.3 (VI), U5.1 (VIN)
VCC: U3.1 (REF), U3.2 (CAT)

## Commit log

2025-05-11 I think halfway there
    [dPicoTracker.kicad_sch]
2025-05-11 add schematic
    [dPicoTracker.kicad_pcb, dPicoTracker.kicad_sch]
2025-05-11 Add power supervisor
    [dPicoTracker.kicad_sch]
2025-05-12 add VFO
    [dPicoTracker.kicad_sch]
2025-05-12 Add everything except pico + headers
    [dPicoTracker.kicad_sch, untitled.kicad_sch]
2025-05-12 add all but pico
    [dPicoTracker.kicad_sch]
2025-05-12 swap to pico
    [dPicoTracker.kicad_pcb, dPicoTracker.kicad_sch, untitled.kicad_sch]
2025-05-13 make pcb
    [dPicoTracker.kicad_pcb, dPicoTracker.kicad_sch]
2025-05-13 Finish PCB i think
    [dPicoTracker.kicad_pcb, dPicoTracker.kicad_sch]
2025-05-14 modify pcb
    [dPicoTracker.kicad_pcb]
2025-05-15 rf tune
    [dPicoTracker.kicad_pcb]
2025-05-16 pcb v1
    [dPicoTracker.kicad_pcb]
2025-05-17 finishing touches
    [dPicoTracker.kicad_pcb, dPicoTracker.kicad_sch]
2025-05-21 finish tracker with dedicated RF
    [dPicoTracker.kicad_pcb]
2025-05-22 add direwolf PCB v1
    [direwolfTracker.kicad_pcb, direwolfTracker.kicad_sch]
2025-05-22 add version no
    [dPicoTracker.kicad_pcb, direwolfTracker.kicad_pcb]
2025-05-23 add BOM
2025-05-24 add BOMs
    [BOM.csv, dPicoTracker.kicad_pcb, direwolfTracker.kicad_pcb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]
2025-05-24 3d models
    [BOM.csv, dPicoTracker.kicad_pcb, direwolfTracker.step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]
2025-05-24 fix crystal
    [dPicoTracker.kicad_sch]
